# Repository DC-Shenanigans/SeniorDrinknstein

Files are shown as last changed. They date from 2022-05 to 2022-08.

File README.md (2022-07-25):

# Se-orDrinknstein

Barbot software reposotory for the Rent an Assassin Party

This robot will be 3 rules safe. 

Porqe es muay rapido. 

Required features: 
- 9 relays for liquor/mixer pumps
- 3 relays for tower light
- 8 functional drink selection buttons (1 or 2 for easter egg)
- One screen for text output (i2c lcd, 20 x 4)
  - Screen will display current status of drink machine
    - Statuses:
      - Ready
      - Pouring
      - Drink done
      - Error

Drink List:

|Drink |Alcohol Amount| Mixer Amount | Button | 
--- | --- | --- | --- |
|Mai Tai| 59mL Rum|118mL Mai Tai Mixer| 0
|Pina Colada|59mL Rum| 118mL Pina Colada Mixer| 1
|Mango Daquiri|59mL Rum|118mL Mango Mixer| 2
|Margarita|59mL Tequila|118mL Marg. Mixer | 3
|Red Wine| 177mL Red Wine| N/A|4
|White Wine| 177mL White Wine| N/A|5
|Water| 177mL Water| N/A | 6
|Water| 177mL Water| N/A| 7

Pump List:

|Pump |Pump Contains|
--- | --- |
|Pump 0 |Rum|
|Pump 1 |Pina Colada Mixer|
|Pump 2 |Mango Daquiri Mixer|
|Pump 3 |Water
|Pump 4 |Tequila|
|Pump 5 |Margarita Mixer|
|Pump 6 |Mai Tai Mixer|
|Pump 7 |White Wine|
|Pump 8 |Red Wine|

GPIO Reference:

|GPIO Pin|Function|drink_name
--- | --- | --- | 
|GPIO 0| Screen - SDA| NA
|GPIO 1| Screen - SCL| NA
|GPIO 2 | Pump | rum 
|GPIO 3 | Pump | pina_colada 
|GPIO 4 | Pump | daqmix 
|GPIO 5 | Pump | water 
|GPIO 6 | Pump | tequila 
|GPIO 7 | Pump | margmix 
|GPIO 16 | Pump | maitaimix 
|GPIO 17 | Pump | whitewine 
|GPIO 19 | Pump | redwine 
|GPIO 8| Selection Button | Mai Tai
|GPIO 9| Selection Button | Pina Colada
|GPIO 10| Selection Button | Mango Daquiri
|GPIO 11| Selection Button | Margarita
|GPIO 12| Selection Button | Red Wine
|GPIO 13| Selection Button | White Wine
|GPIO 14| Selection Button | Water
|GPIO 15| Selection Button | Rum

Button Layout Reference:

[Button Layout](buttons.md)

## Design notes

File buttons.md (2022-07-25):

The HID Buttons are layed out as follows

Top Row, from Left to Right:

Mai Tai | Pina Colada | Mango Daiquiri | Margarita

Bottom Row, from Left to Right:

Red Wine | White Wine | Water | Water

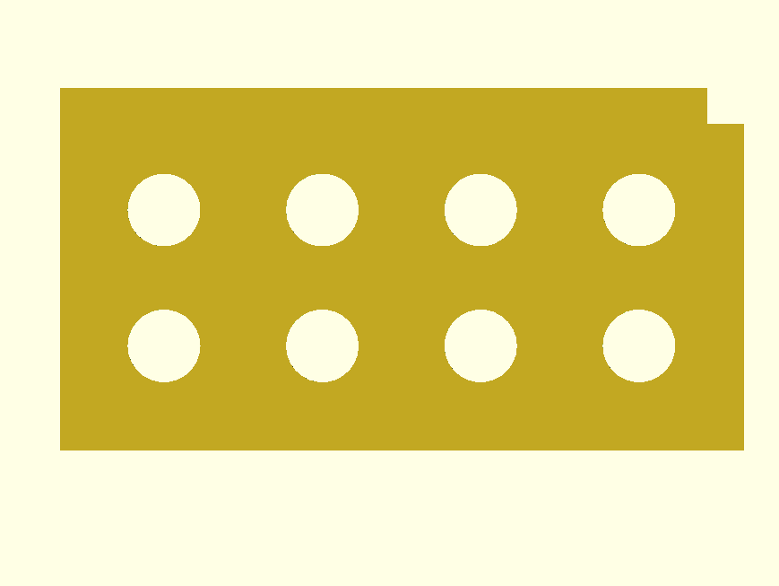
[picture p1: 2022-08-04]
scad_files/senior_drinknstien_baby_face_buttons.png

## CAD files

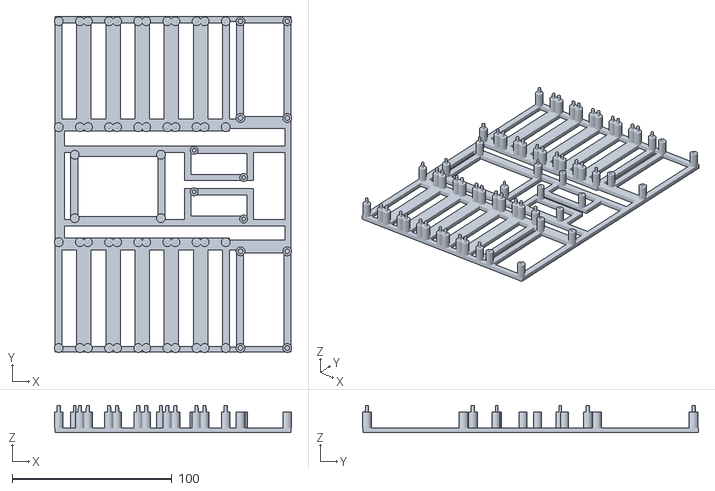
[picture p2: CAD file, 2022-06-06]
scad_files/renders/full_build.stl
148.6 x 210.3 x 17.0

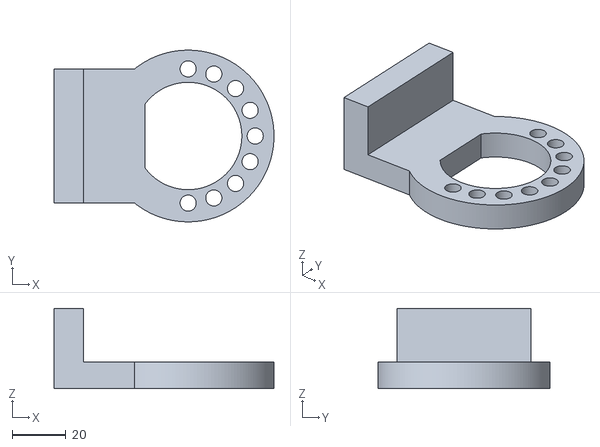
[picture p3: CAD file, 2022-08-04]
scad_files/renders/spout_v0.1.stl
82.0 x 64.0 x 30.0

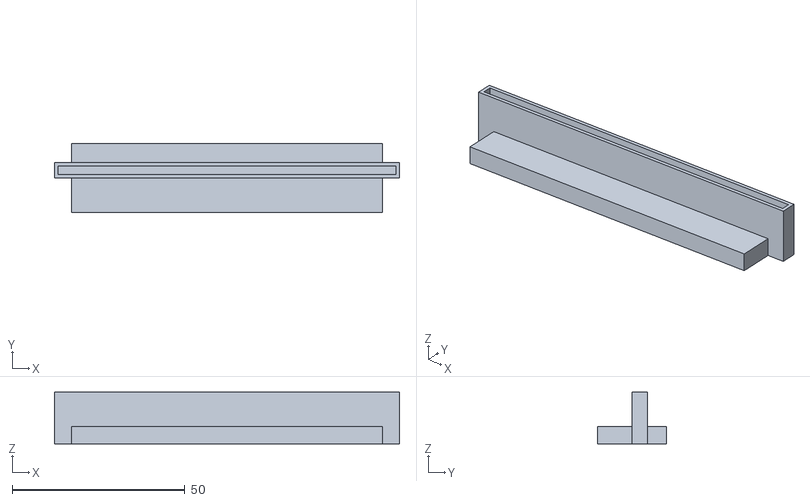
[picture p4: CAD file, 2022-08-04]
scad_files/renders/splashguard_v0.1.stl
100.0 x 20.0 x 15.0

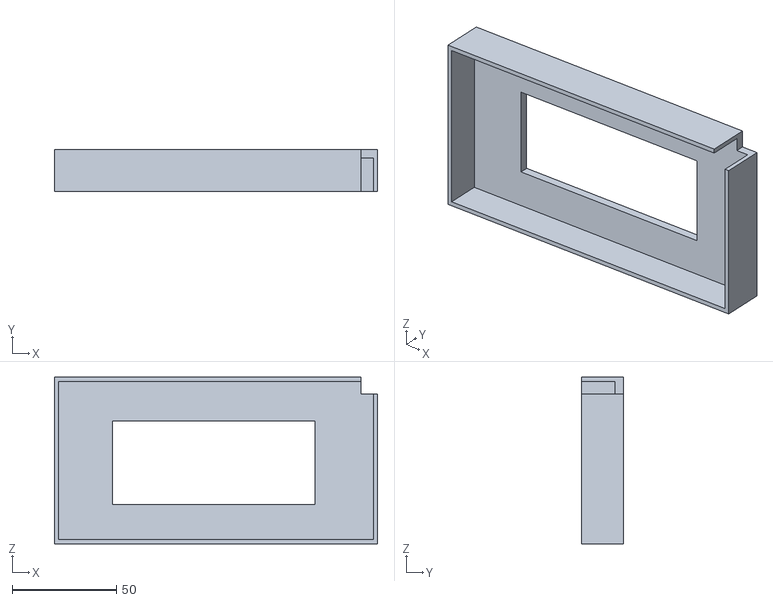
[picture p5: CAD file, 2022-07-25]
scad_files/renders/senior_drinknstien_baby_face.stl
155.0 x 20.0 x 80.0

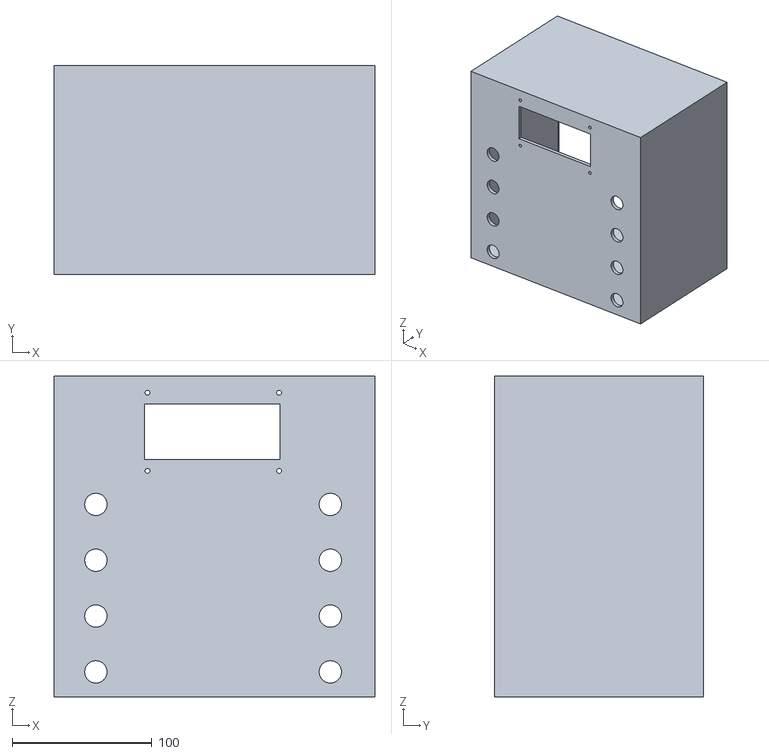
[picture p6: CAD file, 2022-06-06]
scad_files/renders/senior_drinknstien_face_torso.stl
230.0 x 150.0 x 230.0

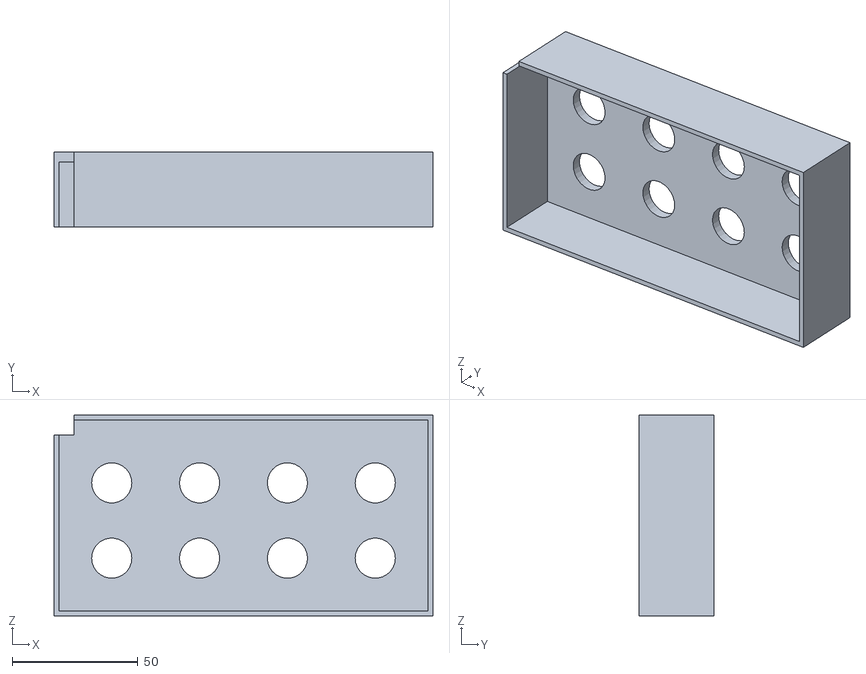
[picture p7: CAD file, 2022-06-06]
scad_files/renders/senior_drinknstien_baby_face_buttons.stl
151.0 x 30.0 x 80.0

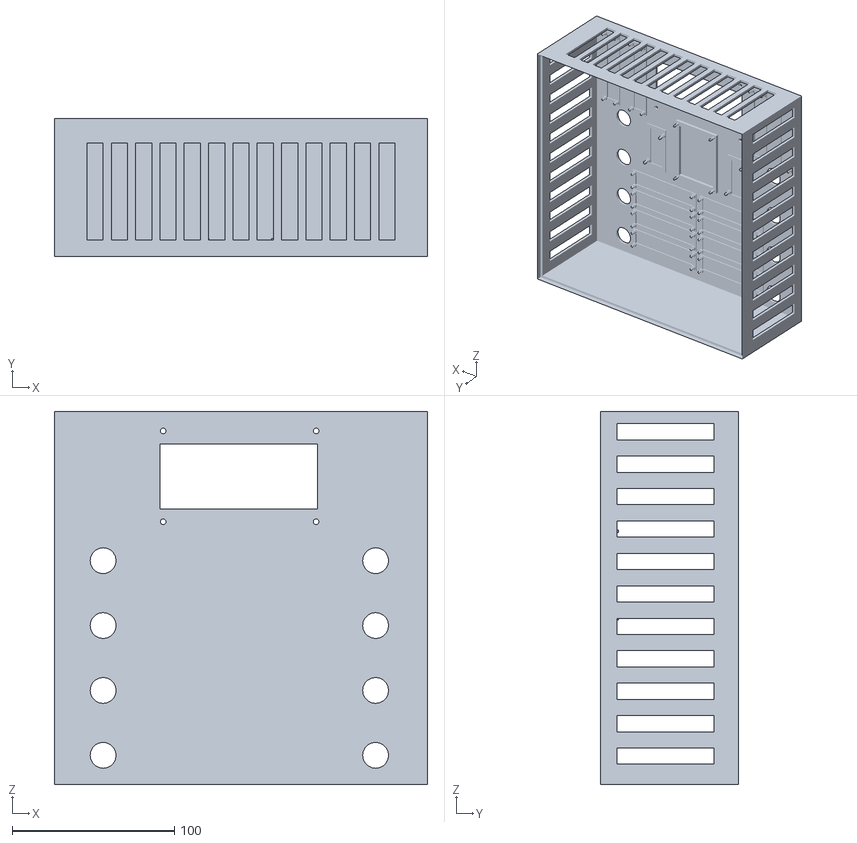
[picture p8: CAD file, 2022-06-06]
scad_files/renders/senior_drinknstien_face.stl
230.0 x 85.0 x 230.0

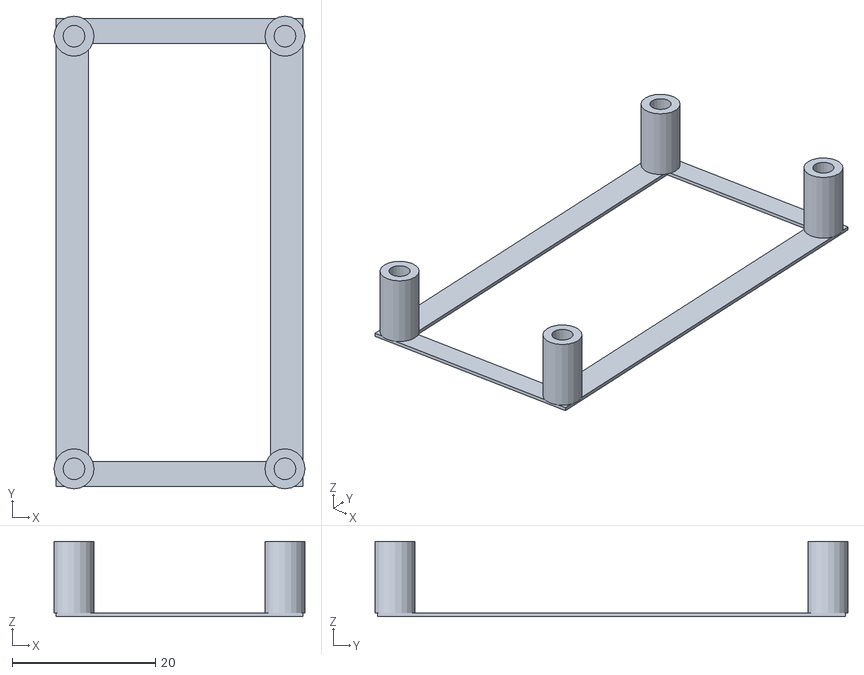
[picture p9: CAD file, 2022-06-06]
scad_files/renders/alt_power_distribution_board.stl
35.1 x 66.1 x 10.5

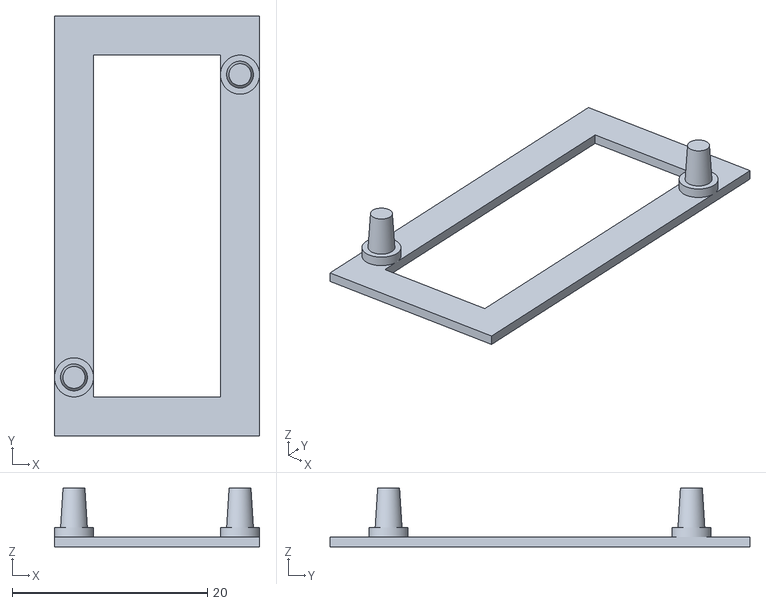
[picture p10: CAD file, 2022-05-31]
scad_files/renders/buck_converter.stl
21.0 x 43.0 x 6.00

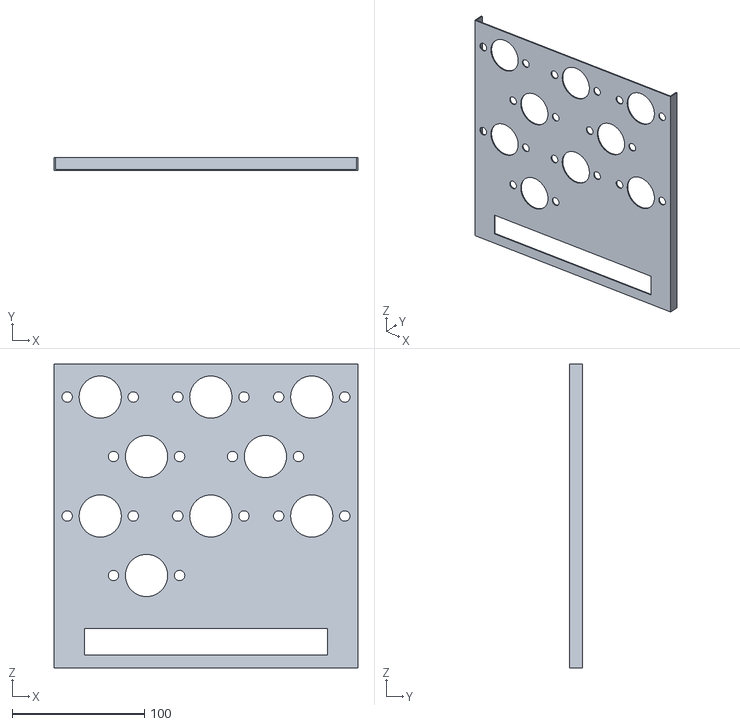
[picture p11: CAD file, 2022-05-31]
scad_files/renders/senior_drinknstien_body.stl
230.0 x 10.0 x 230.0

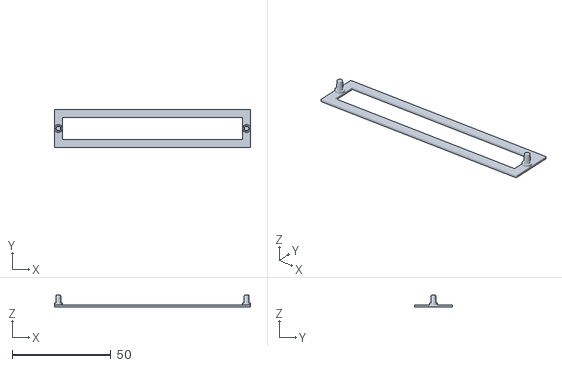
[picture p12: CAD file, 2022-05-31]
scad_files/renders/power_board.stl
99.0 x 19.3 x 6.00

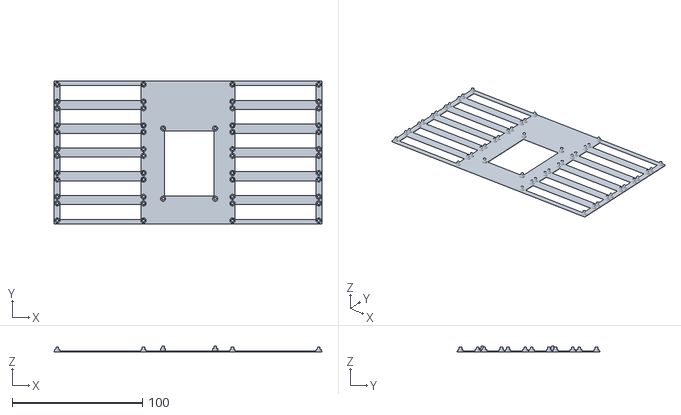
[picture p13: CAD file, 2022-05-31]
scad_files/renders/pico_relay_mount.stl
205.8 x 109.5 x 4.75

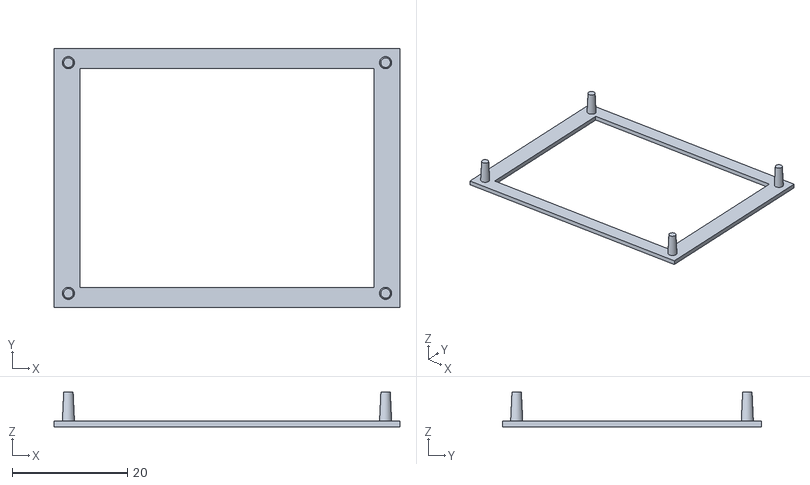
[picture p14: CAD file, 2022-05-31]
scad_files/renders/pi_mount.stl
60.0 x 45.0 x 6.00

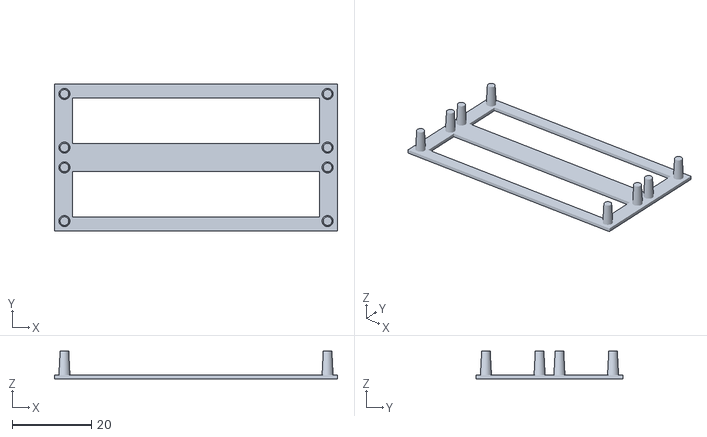
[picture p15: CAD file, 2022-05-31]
scad_files/renders/relay_mount.stl
71.2 x 37.0 x 7.00

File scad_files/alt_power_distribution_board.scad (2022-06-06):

shell_thickness = 1;

$fn = 20;
module power_distribution_board(shell_thickness=1)
{
    standoff_bevel_ratio = .75;
    standoff_radius = 1.85;
        
    safety_standoff_height = 10;
    safety_standoff_radius = 2.8;

    standoff_height = 4 + safety_standoff_height;

    standoff_radius_bevel = standoff_radius * standoff_bevel_ratio;

    pin_hole_separation_x = 29.25;
    pin_hole_separation_y = 60.5;

    base_width_x = pin_hole_separation_x + 5;
    base_depth_y = pin_hole_separation_y + 5;

    standoff_start_x = (base_width_x - pin_hole_separation_x) / 2;
    standoff_start_y = (base_depth_y - pin_hole_separation_y) / 2;

    cutout_start_x = (standoff_start_x + 2);
    cutout_start_y = (standoff_start_y  + 1);

    cutout_width_x = (base_width_x - cutout_start_x * 2);
    cutout_depth_y = (base_depth_y - cutout_start_y * 2);

    standoff_z_offset = shell_thickness - .25;
    difference() 
    {
        cube([base_width_x , base_depth_y, shell_thickness]);

        translate([cutout_start_x,cutout_start_y,-1]) 
        #cube([cutout_width_x, cutout_depth_y,   shell_thickness + 3]);
    }

    // Make the first pin

    
    difference() 
    {
        translate([standoff_start_x,standoff_start_y,shell_thickness]) {
            cylinder(safety_standoff_height,safety_standoff_radius,safety_standoff_radius);
        }
        translate([standoff_start_x,standoff_start_y,shell_thickness]) {
            #cylinder(standoff_height,standoff_radius,standoff_radius_bevel);
        }
    }
    // Make the second pin
    
    difference() 
    {
        translate([standoff_start_x + pin_hole_separation_x,standoff_start_y,shell_thickness]) {
            cylinder(safety_standoff_height,safety_standoff_radius,safety_standoff_radius);
        }
            
        translate([standoff_start_x + pin_hole_separation_x,standoff_start_y,shell_thickness]) {
            #cylinder(standoff_height,standoff_radius,standoff_radius_bevel);
        }
    }
    // Make the third pin
    difference() 
    {
        translate([standoff_start_x ,standoff_start_y+ pin_hole_separation_y,shell_thickness]) {
            cylinder(safety_standoff_height,safety_standoff_radius,safety_standoff_radius);
        }
        translate([standoff_start_x ,standoff_start_y+ pin_hole_separation_y,shell_thickness]) {
            #cylinder(standoff_height,standoff_radius,standoff_radius_bevel);

        }
    }
    // Make the fourth pin

    difference() 
    {
        translate([standoff_start_x + pin_hole_separation_x ,standoff_start_y+ pin_hole_separation_y,shell_thickness]){
            cylinder(safety_standoff_height,safety_standoff_radius,safety_standoff_radius);
        }
        translate([standoff_start_x + pin_hole_separation_x ,standoff_start_y+ pin_hole_separation_y,shell_thickness]){
            #cylinder(standoff_height,standoff_radius,standoff_radius_bevel);
        }
    }

}


//power_distribution_board(shell_thickness=.5);

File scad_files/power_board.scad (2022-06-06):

module power_board(shell_thickness=1)
{
    //shell_thickness = 1;
    standoff_height = 6;
    standoff_bevel_ratio = .75;
    standoff_radius = 1.50;
    standoff_inset = 2;
    
    edge_width = 4;
    edge_width_mod = edge_width * 2;

    standoff_radius_bevel = standoff_radius * standoff_bevel_ratio;

    width = 19.3;
    depth = 98.35;

    difference()
    {
            cube([width, depth, shell_thickness]);
            
            translate([edge_width, edge_width,-1])
            #cube([width - edge_width_mod, depth - edge_width_mod, shell_thickness + 10]);
    }
    translate([width / 2, standoff_inset , shell_thickness]) 
    {
        
        cylinder(standoff_height,standoff_radius,standoff_radius_bevel);
        cylinder(2,2,2);
    }
    translate([ width / 2,depth - standoff_inset, shell_thickness]) 
    {
        
        cylinder(standoff_height,standoff_radius,standoff_radius_bevel);
        cylinder(2,2,2);
    }
}

//power_board();

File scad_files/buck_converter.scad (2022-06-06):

module buck_converter(shell_thickness=1)
{
    //shell_thickness = 1;
    //standoff_height = 6;
    standoff_bevel_ratio = .75;
    standoff_radius = 1.50;
    standoff_inset = 2;
    safety_standoff_height = 10;
    safety_standoff_radius = 2.8;

    standoff_height = 4 + safety_standoff_height;
    safety_standoff_radius = 2.5;
    edge_width = 4;
    edge_width_mod = edge_width * 2;

    standoff_radius_bevel = standoff_radius * standoff_bevel_ratio;

    depth = 43;
    width = 21;

    difference()
    {
            cube([width, depth, shell_thickness]);
            
            translate([edge_width, edge_width,-1])
            #cube([width - edge_width_mod, depth - edge_width_mod, shell_thickness + 10]);
    }
    difference(){
        translate([width - standoff_inset, 37, shell_thickness]) 
        {
        cylinder(safety_standoff_height,safety_standoff_radius,safety_standoff_radius);
        }
        translate([width - standoff_inset, 37, shell_thickness]) 
        {
            #cylinder(standoff_height,standoff_radius,standoff_radius_bevel);
        }
    }
    difference(){
        translate([standoff_inset, 6, shell_thickness]) 
        {
        cylinder(safety_standoff_height,safety_standoff_radius,safety_standoff_radius);
        }
        translate([standoff_inset, 6, shell_thickness]) 
        {
            
            #cylinder(standoff_height,standoff_radius,standoff_radius_bevel);
        }
    }
}

//buck_converter();

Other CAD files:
scad_files/renders/full_build_screws.stl
scad_files/button_cutout.scad
scad_files/TEST.scad
scad_files/display_mount.scad
scad_files/full_build.scad
scad_files/pi_mount.scad
scad_files/pump_mount.scad
scad_files/relay_mount.scad
scad_files/senior_drinknstien_baby_face.scad
scad_files/senior_drinknstien_baby_face_buttons.scad
scad_files/senior_drinknstien_body.scad
scad_files/senior_drinknstien_face.scad
scad_files/splashguard.scad
scad_files/tube_holder.scad

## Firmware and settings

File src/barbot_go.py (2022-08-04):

# All rights are yours to do what you want with.
# I can't stop you, I'm just pixels on a screen.

import re
import time
from src.configs import load_from_json
from src.gpio import BasicGPIO
from src.screen import ScreenGo
from src.logwas import fuck         # Log was fuck


class BarbotGo():
    run_mode = None

    def __init__(self, mode="CONSOLE"):
        # Init screen
        self.screen = ScreenGo()

        # Set mode for some reason even though i'm going to require a screen
        self.run_mode = mode

        self.basic_gpio = BasicGPIO()
        
        # Print startup message
        self.print_to_display(
            "Starting up         \
Dr. McGillicutty's  \
Magic Drink Elixir  \
Mixer               ")

        self.drink_list = load_from_json("drinks_config.json")
        
        # See if we're in purge mode
        if self.basic_gpio.button_settings[f'GP13']["object"].value:
            self.basic_gpio.toggle_pin_state("red")
            self.purge_mode()
        
        # See if we're in mapping mode
        if self.basic_gpio.button_settings[f'GP14']["object"].value:
            self.basic_gpio.toggle_pin_state("red")
            self.basic_gpio.toggle_pin_state("green")
            self.button_mapping_mode()
        
        # self.button_mapping_mode()

        # prepare logger
        # There is something up with the truncate here :/
        self.log = fuck("stats.json")

        # Turn on the green light baby
        #time.sleep(5)


                
        self.basic_gpio.toggle_pin_state("green")
        self.idle_message = "Dr. McGillicutty's  \
Magic Drink Elixir  \
Mixer               \
Ready to mix!      "
        self.print_to_display(self.idle_message)
    
    def button_mapping_mode(self):
        self.print_to_display("Entering BUTTON MAPPING mode, one moment...")
        run_loop = True
        self.print_to_display("Now in BUTTON MAPPING mode BEEP BOOP BOP BEEEEEEP")
        count = 0
        while(run_loop):
            count +=1
            if count % 5000 == 0:
                self.print_to_display("Get back to mappin why don't ya!", True)

            for target_gpio in self.basic_gpio.button_settings:
                if self.basic_gpio.button_settings[f'{target_gpio}']["object"].value:
                    self.print_to_display(f"Button {target_gpio} was being pressed", True)
                    if self.basic_gpio.button_settings['GP8']["object"].value == True \
                        and self.basic_gpio.button_settings['GP9']["object"].value == True:
                        self.print_to_display("Exiting Mapping Mode ^_^")
                        run_loop = False
                    

    def purge_mode(self):
        self.print_to_display("Entering PURGE mode, one moment...")
        time.sleep(1)

        run_loop = True
        self.print_to_display("PURGE mode ENABLED")
        while(run_loop):
            for target_gpio in self.basic_gpio.button_settings:
                if self.basic_gpio.button_settings[f'{target_gpio}']["object"].value:
                    self.print_to_display(f"Button {target_gpio} is being pressed", True)
                    button_map = {
                        "GP8":"GP2",
                        "GP9":"GP3",
                        "GP10":"GP4",
                        "GP11":"GP5",
                        "GP12":"GP6",
                        "GP13":"GP7",
                        "GP14":"GP16",
                        "GP15":"GP17"
                    }
                    if self.basic_gpio.button_settings['GP8']["object"].value == True \
                        and self.basic_gpio.button_settings['GP9']["object"].value == True:
                        self.print_to_display("You escaped the PURGE! Now have a drink on Dr. McGillicutty ^_^")
                        run_loop = False
                    if self.basic_gpio.button_settings['GP8']["object"].value == True \
                        and self.basic_gpio.button_settings['GP12']["object"].value == True:
                        self.print_to_display("I'm sorry Dave, I can't let you do that")
                    if self.basic_gpio.button_settings['GP8']["object"].value == True \
                        and self.basic_gpio.button_settings['GP13']["object"].value == True:
                        self.print_to_display("PROTIP: Aask me no questions and I'll tell you no lies")
                    else:
                        liquor = self.basic_gpio.pin_settings[button_map[target_gpio]]["drink"]
                        if liquor == "malort":
                            self.print_to_display("KILL ALL HUMANS")
                        else:
                            self.print_to_display(f"Purging {liquor}....")

                        self.basic_gpio.purge_mode(target_gpio, button_map[target_gpio])

                        if liquor == "malort":
                            self.print_to_display("Thank you for using Dr. McGillicutty's Suicide Booth!")
                        else:
                            self.print_to_display(f"Done purging Dr. McGillicutty's {liquor}!")

                        self.print_to_display("PURGE mode ENABLED", immediate=True)

    def main_menu(self):
        if(self.run_mode == "CONSOLE"):
            for idx, item in enumerate(self.drink_list):
                print("%d %s" % (idx, item["name"]))
            user_input = input("Please select a drink: ")
            try:
                self.drink_selection = self.drink_list[int(user_input)]
                self.make_drink()
            except Exception as e:
                self.print_to_display(f"NOT A VALID OPTION. {e}")
        else:
            # Poll the buttons
            for target_gpio in self.basic_gpio.button_settings:
                if self.basic_gpio.button_settings[f'{target_gpio}']["object"].value:
                    self.print_to_display(
                        f"Button {target_gpio} is being pressed", True)
                    drink = self.basic_gpio.button_settings[f'{target_gpio}']["drink"]
                    for item in self.drink_list:
                        if drink == item["name"]:
                            article = "an" if re.search("^[AaEeIiOoUu]", drink) else "a"
                            self.print_to_display(f"This is {article} {drink}")
                            self.drink_selection = item
                            self.make_drink()

                    time.sleep(0.5)

    def print_to_display(self, text, immediate = False, letter_sleep = 0.01):
        # Clear the screen
        self.screen.write_to_screen(text, immediate, letter_sleep)
        print(text)
        # print("IDKWTFUDO, DO IT BETTER")

    def make_drink(self):
        self.print_to_display(f"Making {self.drink_selection['name']}...")

        # Set tower light to RED and turn off GREEN
        self.basic_gpio.toggle_pin_state("green")
        self.basic_gpio.toggle_pin_state("red")
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

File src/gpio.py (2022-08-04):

import board
import digitalio


class BasicGPIO():
    def __init__(self):
        print("setting up basic GPIO")
        
        self.pin_settings = {}
        self.pin_settings["GP2"] = {"pin": board.GP2, "drink": "rum"}
        self.pin_settings["GP3"] = {"pin": board.GP3, "drink": "pina_colada"}
        self.pin_settings["GP4"] = {"pin": board.GP4, "drink": "daqmix"}
        self.pin_settings["GP5"] = {"pin": board.GP5, "drink": "water"}
        self.pin_settings["GP6"] = {"pin": board.GP6, "drink": "tequila"}
        self.pin_settings["GP7"] = {"pin": board.GP7, "drink": "margmix"}
        self.pin_settings["GP16"] = {"pin": board.GP16, "drink": "maitaimix"}
        self.pin_settings["GP17"] = {"pin": board.GP17, "drink": "whitewine"}
        self.pin_settings["GP19"] = {"pin": board.GP19, "drink": "redwine"}
        self.pin_settings["green"] = {
            "pin": board.GP20, "color": "green", "status": False, "mode": None}
        self.pin_settings["red"] = {
            "pin": board.GP21, "color": "red", "status": True, "mode": "solid"}
        self.pin_settings["loud"] = {
            "pin": board.GP22, "color": "loud", "status": False}

        self.button_settings = {}
        self.button_settings["GP8"] = {"pin": board.GP8, "drink": "Water"}
        self.button_settings["GP9"] = {"pin": board.GP9, "drink": "White Wine"}
        self.button_settings["GP10"] = {"pin": board.GP10, "drink": "Red Wine"}
        self.button_settings["GP11"] = {"pin": board.GP11, "drink": "Mai Tai"}
        self.button_settings["GP12"] = {"pin": board.GP12, "drink": "Pina Colada"}
        self.button_settings["GP13"] = {"pin": board.GP13, "drink": "Margarita"}
        self.button_settings["GP14"] = {"pin": board.GP14, "drink": "Water"}
        self.button_settings["GP15"] = {"pin": board.GP15, "drink": "Mango Daquiri"}

        self.initialize_gpio()

    def initialize_gpio(self):
        for target_gpio in self.pin_settings:
            self.initialize_digital_output(target_gpio)
        for target_gpio in self.button_settings:
            self.initialize_button_pull_down(target_gpio)
        led = digitalio.DigitalInOut(board.LED)
        led.direction = digitalio.Direction.OUTPUT
        led.value = True

    def initialize_button_pull_down(self, target_gpio):

        if "object" in self.button_settings[f'{target_gpio}']:
            print("Already initialized pin!!!")
            return None

        if (target_gpio in self.button_settings):
            self.button_settings[f'{target_gpio}']["object"] = digitalio.DigitalInOut(
                self.button_settings[f'{target_gpio}']["pin"])
            self.button_settings[f'{target_gpio}']["object"].switch_to_input(
                pull=digitalio.Pull.DOWN)

        else:
            print("NOT A VALID PIN")

    def initialize_digital_output(self, target_gpio):
        if ("object" in self.pin_settings[f'{target_gpio}']):
            print("Already initialized pin!!!")
            return None

        if (target_gpio in self.pin_settings):
            self.pin_settings[f'{target_gpio}']["object"] = digitalio.DigitalInOut(
                self.pin_settings[f'{target_gpio}']["pin"])
            self.pin_settings[f'{target_gpio}']["object"].direction = digitalio.Direction.OUTPUT

        else:
            print("NOT A VALID PIN")

    def toggle_pin_state(self, target_gpio):
        if(self.pin_settings[f'{target_gpio}']["object"].value is True):
            self.pin_settings[f'{target_gpio}']["object"].value = False
        else:
            self.pin_settings[f'{target_gpio}']["object"].value = True
    
    def purge_mode(self, button_gpio, relay_gpio):
        # set the gpio to high while the button is held
        while(self.button_settings[f'{button_gpio}']["object"].value == True):
            self.pin_settings[relay_gpio]["object"].value = True
        self.pin_settings[relay_gpio]["object"].value = False
        

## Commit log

2022-05-09 Refactored and fixed the json loading function
    [configs.py]
2022-05-09 Fix file error handling
    [configs.py]
2022-05-09 Updated json load error with filename
    [configs.py]
2022-05-20 Adding base code for relay mount
    [relay_mount.scad]
2022-05-20 gpio and pin handling set up
    [relay_mount.scad]
2022-05-27 adding models
    [buck_converter.scad, full_build.scad, pi_mount.scad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]
2022-05-27 adding almost working screen
    [relay_mount.scad]
2022-05-27 Updating designs for matching realith
    [buck_converter.scad, power_board.scad]
2022-05-27 Finished debugging, all we have to do now is make sure we hook up all the relays correctly :)
    [barbot_go.py]
2022-05-31 updating ux
    [buck_converter.scad, buck_converter.stl, full_build.scad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]
2022-06-03 Adding updated models
    [buck_converter.scad, button_cutout.scad, display_mount.scad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]
2022-06-06 Adding recent model changes
    [TEST.scad, alt_power_distribution_board.scad, buck_converter.scad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]
2022-06-06 Adding recent renders
    [alt_power_distribution_board.stl, buck_converter.scad, full_build.scad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]
2022-06-06 Adding recent face changes
    [senior_drinknstien_baby_face.stl]
2022-06-09 Pretty print
2022-06-10 Adding recent changes
    [full_build_screws.stl, pi_mount.scad, relay_mount.scad]
2022-06-11 Adding render
    [senior_drinknstien_baby_face.stl]
2022-06-12 Update README.md
    Updated drinks, pump numbers, and added GPIO reference.
2022-06-14 Updating face
    [display_mount.scad, senior_drinknstien_baby_face.scad]
2022-06-15 Fix logwas.py. Functions now tested
    [logwas.py]
2022-06-15 Update barbot_go to log drink and pump stats
2022-07-25 Almost ready for the big show
    [button_cutout.scad, senior_drinknstien_baby_face.stl]
2022-08-04 READY FOR SERVICE. PORQE ES MUY RAPIDO
    [splashguard.scad, splashguard_v0.1.stl, spout_v0.1.stl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]
